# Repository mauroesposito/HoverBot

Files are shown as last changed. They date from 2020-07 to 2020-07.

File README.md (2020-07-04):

My construction of this fantastic robot.

Here the final result:

hoverbot

Next steps/improvements:  

* improve security: add kill switch using channel 4 of the rc receiver;
* adding a power switch to stop current to ODrive from battery: as activation of kill switch command from arduino (or -- see next);
* alternatively evaluate solution to send a command to ODrive to stop immediately power erogation to motors;
* simplify pid configuration: adding an ESP32 with a web interface with Arduino to make easy and painless calibration of the parameters.

Thank you Lukas for this fantastic robot.

Mauro

***

# HoverBot
Rugged radio-controlled self-balancing robot using hoverboard hub motors.

HoverBot_Slide

## Table of contents
1. [Key Components](#components)
2. [External Dependencies](#dependencies)
3. [Videos](#video)
4. [Control Scheme](#control)
5. [Schematic](#schematic)
6. [Wiring](#wiring)
    1. [ODrive](#odrive)
    2. [IMU](#imu)
    3. [RC Receiver](#receiver)
    4. [Arduino](#arduino)
7. [Press](#press)
8. [Additional Documentation](#additional)

## Key Components 
* An Arduino Mega https://store.arduino.cc/mega-2560-r3. Using the Mega because the project needs three hardware interrupt pins to decode the RC receiver's PWM signals.
* A Bosch BNO055 IMU https://www.adafruit.com/product/2472. Gives ready-to-use tilt angle estimation as well as gyro and accelerometer raw readings.
* An ODrive motor controller (48V) https://odriverobotics.com/shop/odrive-v35. Enables very smooth current control for the two motors.
* Two hoverboard hub motors (easy to source from ebay). Very affordable, powerful and easy-to-use motors.

## External Dependencies 
* Metro https://github.com/LuSeKa/Metro
* ODriveArduino https://github.com/madcowswe/ODrive
* Adafruit_Sensor https://github.com/adafruit/Adafruit_Sensor
* Adafruit_BNO055 https://github.com/adafruit/Adafruit_BNO055

## Videos 
YouTube Video (https://www.youtube.com/watch?v=QNOgWHhilm4)
YouTube Video (https://www.youtube.com/watch?v=jp_vRK7mbwY)

## Control Scheme 
The ODrive is operated in current control mode. The current is computed by the Arduino from the pitch and pitching velocity to control balancing, from the throttle command to control the forward and backward velocity, and from the steering command and the yaw velocity to control the steering. The controller is tuned with five parameters listed in the config.h file.

HoverBot_control

A problem of this control scheme is that the onboard controller does not get velocity feedback. If the vehicle goes too fast, the balance controller cannot compensate a forward fall anymore, and it will fall over eventually. The human at the sticks therefore needs to make sure that the velocity is kept sufficiently slow.

## Schematic 
The following diagram roughly explains the data flow and types of electrical connections.
HoverBot_wiring

## Wiring 

Note that the wiring is *Highly Experimental* and just a *Proof-of-Concept*.
wiring_overview
Wiring

The wiring connects the wheel motors and their hall sensors with the ODrive, the ODrive to the Arduino and the Arduino to the IMU (sitting on a breadboard) and to the RC receiver.

### ODrive 
ODrive_wiring

The wiring of the ODrive is explained on the ODrive website (that has very nice docs overall!):
https://docs.odriverobotics.com/#wiring-up-the-odrive
#### Power and motors
The ODrive is powered from the battery via its DC clamps (thick black and red cables on the left), and each motor's three phases (A, B, C, blue, yellow and green) are connected to one of its motor output clamps (M0 and M1). The order in which the motor wires are connected does not matter, the ODrive figures this out by itself during calibration.
#### Auxiliary resistor
If HoverBot is powered from batteries without built-in battery management system (PMS), no auxiliary breaking resistor is required (the ODrive dumps recuperated energy into the battery). If the batteries have a PMS (such as the ones usually found in a hoverboard), using the auxiliary resistor might prevent overvoltage errors.
#### Hall sensors
Each hoverboard motor comes with hall sensors that tell the ODrive when to power which of the three phases. Each hall sensor has five wires: Two for power (5V, usually red and GND, usually black) and three for signal (often blue, yellow and green). A motor's hall sensors are connected using extension cables to the corresponding sensor inputs (M0 and M1) on the ODrive's J4 connector. The three signal lines are connected to inputs A, B and Z where the order again does not matter. Note that it might be necessary (depending on the version of the ODrive) to add some a 22nF capacitor between each of the three signals and ground for signal integrity (insulated with hot glue), as is mentioned here:
https://discourse.odriverobotics.com/t/encoder-error-error-illegal-hall-state/1047/6
#### 5V power
The ODrive powers the 5V power supply of all other components, so its GND (black cable on the J3 connector) and 5V (red cable on the J2 connector) are connected to a breadboard that acts as power distribution.
#### UART
The ODrive communicates with the Arduino via the serial port, or UART. The UART pins are GPIO 1 (yellow) and GPIO 2 (white), as explained here (GPIO 1 connects to the Arduino's RX, GPIO 2 to the Arduino's TX):
https://docs.odriverobotics.com/interfaces#ports

### IMU 
IMU_wiring
The IMU only requires two wires for 5V power (red) and GND (black) from the breadboard and two wires for the I2C connection to the Arduino, connecting the IMU's and the Arduino's SDA (white) and SCL (left green). https://learn.adafruit.com/adafruit-bno055-absolute-orientation-sensor/pinouts

### RC Receiver 
receiver_wiring

The receiver is powered by 5V (red) and GND (blue) from the breadboard and each of the PWM signal outputs (three for the HoverBot) are connected to one of the Arduino's inputs that are capable of hardware interrupts. The fact that three hardware interrupt pins are needed is the reason why HoverBot uses an Arduino Mega rather than a smaller and cheaper Uno or Nano (see https://www.arduino.cc/reference/en/language/functions/external-interrupts/attachinterrupt/). The pins used are 2 (orange), 3 (yellow) and 18 (green), and their channel assignment is set in the first lines of the config.h file: https://github.com/LuSeKa/HoverBot/blob/master/config.h

### Arduino 
The Arduino is powered from 5V (red) and GND (black) from the breadbaord. Apart from the connections already mentioned, the Arduino's USB port should be accessible for programming.

## Press 
* [IEEE Spectrum Video Friday](https://spectrum.ieee.org/automaton/robotics/robotics-hardware/video-friday-agility-robotics-humanoid-robot-digit-stroll-downtown) (07 June 2019)
* [Arduino Blog](https://blog.arduino.cc/2019/06/10/hoverboard-motors-turned-into-an-rc-skater/) (10 June 2019)
* [Weekly Robotics #45](https://weeklyrobotics.com/weekly-robotics-45) (30 June 2019)

## Additional Docs 
* [How To HoverBot](https://docs.google.com/document/d/1BMKzhPN70OgQfNl87zCoNQgiD5hnJ96jCFjzUalukxU/edit?ts=5ce60720#)
* [ODrive Forum](https://discourse.odriverobotics.com/t/hoverbot-self-balancing-vehicle-with-hoverboard-wheels/2249)

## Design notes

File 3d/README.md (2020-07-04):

# 3D components

Here you can found some printed parts that I've used to make this robot.
Resources that I've used to make this robot:
* 40mm elluminium extrusion: to keep motor axle blocked;
* wood bars 40mm x 10mm in section;
* perforated plates to assempbly the base of the robot;
* lot of T-Nut M5 (for aluminium extrusion fix) and 30mm roudend head M5 hexagonal bolts for vertical and horizontal parts.

### Battery holder
Battery holder, for LiPO 6s:

immagine

To join the parts, you can use one of these 3 solutions:
* use some little stick in the holes;
* use some glue
* use a velcro strip to keep the parts closed

I suggest to use the third way: with velcro strip you add more strenght to keep battery safe on robot:


### Motor axle keeper
To keep safe the motor rotor axle on the 40mm aluminium extrusion, I've used [this object](https://www.thingiverse.com/thing:2990353), and here the final result:



### Vertical wood holder

Here the vertical wood holder, you need 2 of this:

Annotazione 2019-07-22 100806


### Horizontal wood holder

Here the horizontal wood holder, you need 6 of this:

Annotazione 2019-07-22 100652


### Final result

Some picture of the robot assembly details:







I've added a horizontal wood bar to keep robot in vertical position when is off:


And don't forget to add some pluriball on the head robot to avoid violent crashes on the ground (yes, it can occur sometimes):


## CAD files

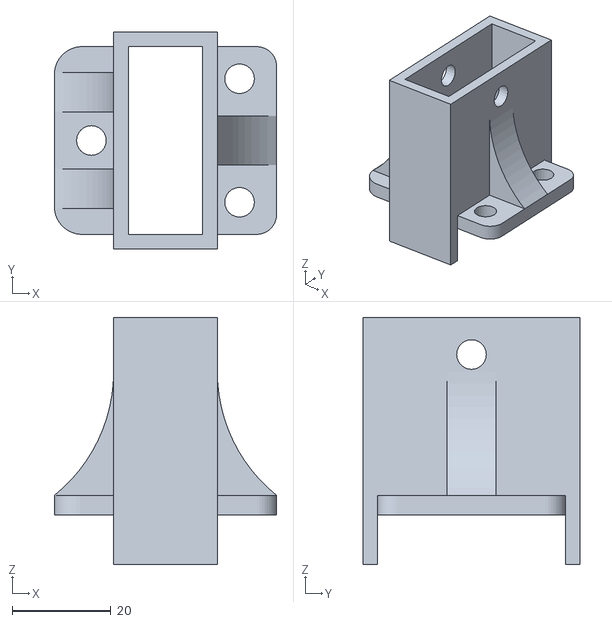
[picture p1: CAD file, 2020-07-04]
3d/horizontal_wood_holder.stl
45.0 x 44.0 x 50.0

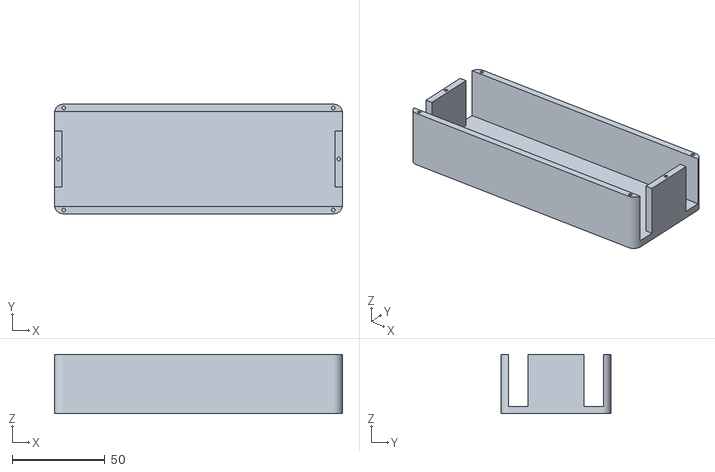
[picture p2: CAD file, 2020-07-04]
3d/case_lipo_6s -cover.stl
155.0 x 59.0 x 32.0

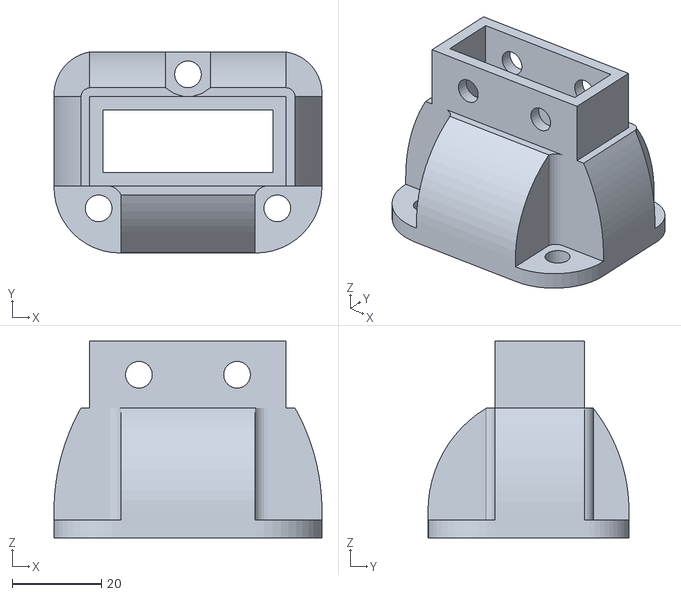
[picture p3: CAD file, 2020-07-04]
3d/vertical_wood_holder.stl
60.0 x 45.0 x 44.0

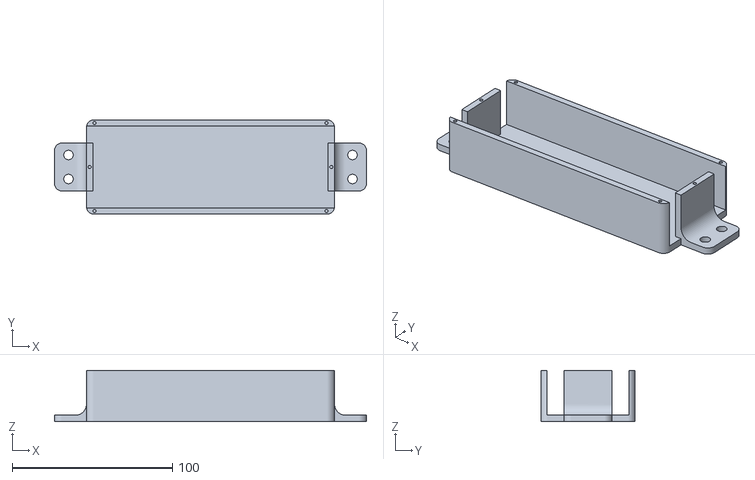
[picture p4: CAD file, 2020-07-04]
3d/case_lipo_6s -base.stl
195.0 x 59.0 x 32.0

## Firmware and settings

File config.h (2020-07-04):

/*
 * General configuration for HoverBot.ino
 * Tested on an Arduino Mega
 */

// HARDWARE
#define PWM_CHANNEL_1 2
#define PWM_CHANNEL_2 3
#define PWM_CHANNEL_3 18
#define LEDPIN 13

#define MOTORDIR_0 1    // Lukas default: -1
#define MOTORDIR_1 -1   // Lukas default: 1


/**
 * Note by Lukas in: 
 * - https://docs.google.com/document/d/1BMKzhPN70OgQfNl87zCoNQgiD5hnJ96jCFjzUalukxU/edit?ts=5ce60720#
 * in "Controller Tuning"
 * **
 * The controller is based on five parameters:
    KP_BALANCE: Determines how much the robot reacts to leaning forward or backward. 
                A high value might lead to tilt oscillations
    KD_BALANCE: Determines how much the robot reacts to the rate of tilt change. 
                It generally dampens oscillations, but a value too high might lead to increased 
                oscillations (mainly due to time lags in the control loop)
    KP_POSITION: Determines how strongly the robot reacts to RC throttle commands
    KP_STEERING: Determines how strongly the robot reacts to RC steering commands
    KD_ORIENTATION: Determines how much the robot tries to counteract turning around 
                    the vertical axis - higher values make going straight easier but turning slower
 */
// CONTROLLER
#define KP_BALANCE 0.35       // Lukas default: 0.4
#define KD_BALANCE  -0.03     // Lukas default: -0.065
#define KP_POSITION 0.015     // Lukas default: 0.015       
#define KP_STEERING 0.01      // Lukas default: 0.01
#define KD_ORIENTATION -0.01  // Lukas default: 0.01; my robot enter in loop on vertical axis: try also 0.001
#define TILT_LIMIT 40

// RADIO CONTROL
#define ENGAGE_THRESHOLD 1500
#define PWM_CENTER 1500

// SCHEDULING
#define BLINK_INTERVAL 200
#define CONTROLLER_INTERVAL 10
#define ACTIVATION_INTERVAL 50

// SERIAL
#define BAUDRATE_ODRIVE 115200
#define BAUDRATE_PC 115200

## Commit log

2019-08-30 FIX: update some controller values to work on my configuration.
    [config.h]
2020-07-04 ADD: added my bot PID values.
2020-07-04 ADD: added 3d parts and some pictures of final robot assembly.
    [case_lipo_6s -base.stl, case_lipo_6s -cover.stl, horizontal_wood_holder.stl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]
